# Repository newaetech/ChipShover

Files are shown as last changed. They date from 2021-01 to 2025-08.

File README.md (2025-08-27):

# ChipShover®

ChipShover is an XYZ table &amp; driver, with handy Python interface. It's designed for close analysis of ICs using tools like Electromagnetic Fault Injection (EMFI), EM Probes for side-channel, and more. In both specifications and cost it falls somewhere between between 3D printers & microscope stages.

ChipShover consists of the following main parts:

* Physical XYZ Stage (based on stepper motors)
* Interposers to mount tools onto the stage
* Controller for XYZ stage (based on open-source Marlin firmware)
* Python interface on computer

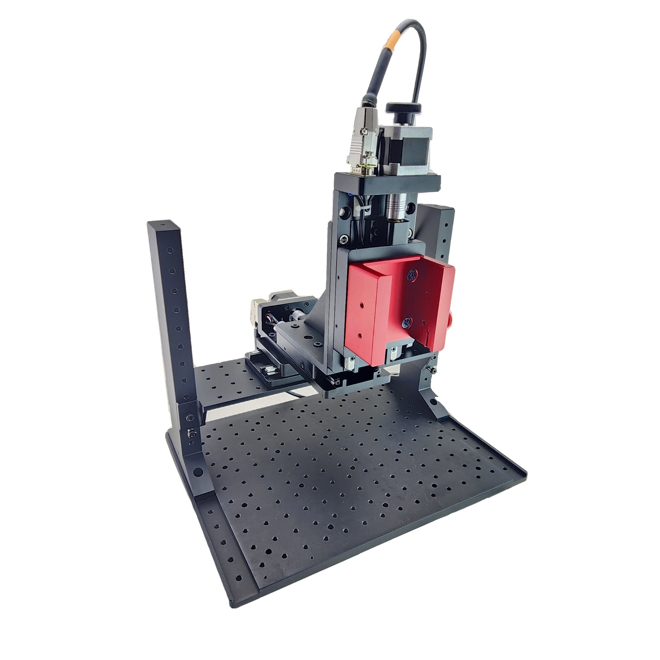
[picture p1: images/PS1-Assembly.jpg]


## Physical XYZ Stage

The physical XYZ stage is designed for two major variants, however you can easily customize it based on tables and parts you have on-hand. These variants are presented to simplify your general choice of options. They are currently called the *medium-resolution* stage (step size of 156.25 nm, backlash/general error around 3um), and a low-resolution stage (step size of 781.25 nm, bkaclash/general error around 50-100 um).

### Medium-Resolution Stage (< 1 um)

The medium-resolution stage is composed of a custom frame and motorized microscope stages. The frame is made entirely of solid machined aluminum.

For easiest setup and best results. This stage is available as part of a Kit from NewAE that also includes our controller, power supply, and helpful accesories. We call it the ChipShover PS1 (Positining system 1). 

### Low-Resolution Stage

The low-resolution stage uses a CNC frame fairly widely available on AliExpress and similar. With this version you must buy the stage yourself - the size and lowish cost ($500) of the stage makes it not worth carrying for NewAE! The cost is significantly lower, with more hassle in the purchasing process and somewhat lower resolution and specifications on the resulting table.

## Interposers

The XYZ stage is designed to fit a variety of tools using a 50x50mm bolt pattern. Currently, this has the following interposers:

* ChipSHOUTER® holder.
* Pen-Style EM probe holder.

The ChipSHOUTER mounting hardware is included in the PS1 kit, otherwise these interposers can be 3D printed or machined from files in the repo.

## Controllers

The controller is based on 3D printer controllers which have extensive community resources behind their hardware and firmware. The ChipShover controller is specifically based on the Arduino DUE, which uses a Microchip SAM3X (we use the similar SAM3U in many of our products already which was our reasoning).

The firmware is open-source and is a [build of Marlin2 with a custom board type](https://github.com/newaetech/ChipSHOVER-Marlin). The board is designed to be the ChipShover-One ($1300 for enclosed & tested unit, lower-cost version planned around ~$350). Other boards such as the [Archim2](https://ultimachine.com/products/archim2) are possible with some limitations (approx $180 for board + some cables needed).

### ChipShover-One

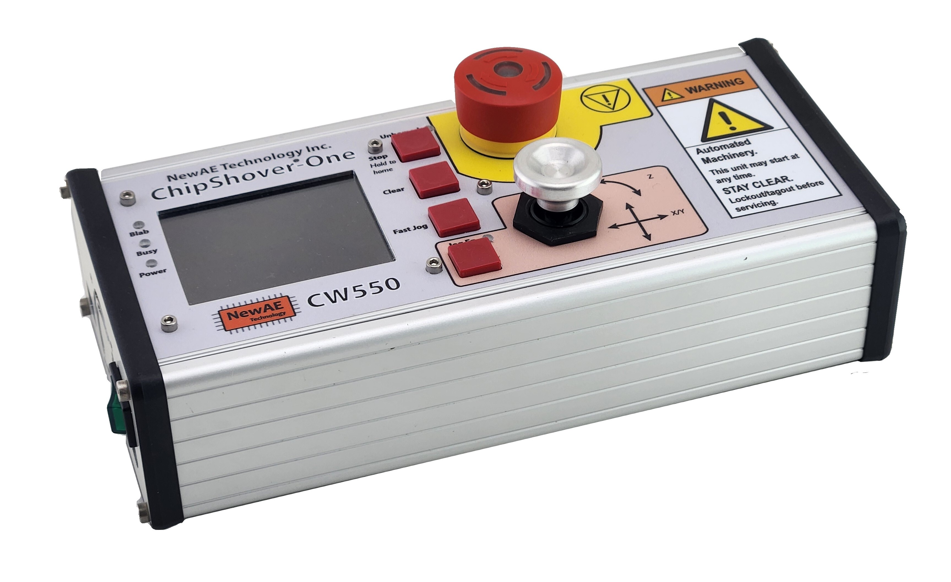
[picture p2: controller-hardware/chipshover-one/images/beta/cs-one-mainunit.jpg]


The ChipShover-One is our own stepper controller. While there are hundreds of already existing controllers out there, we figured why not make it interesting with our own take? Several feature relevant to the ChipShover usage that are not widely available in existing 3D printer driver boards were specifically added:

* 3 endstop inputs per axis (2 endstops, 1 higher-resolution home).
* Swappable driver boards to work with different tables.
* Easy user API over USB (Ethernet optional).
* Higher drive current (~2.4A).
* Extension connectors for each axis (currently RS485 + I2C + single GPIO used for "stop" input).
* Physical E-Stop button that disconnects power to motors.
* User interface including colour LCD.

As there are *hundreds* of low-cost open-source stepper controllers out there, the ChipShover-One hardware is not *currently* released as full OSHW. Schematics and other information *is* available for your use already. As we finish releasing this it's likely ChipShover-One will become more open.

### Archim2

The Archim2 board is an open-source hardware controller board. It is [sold by UltiMachine](https://ultimachine.com/products/archim2) and can be used to make a board that is compatible with the ChipShover Python API.

The primary limitation of the Archim2 is a lower default resolution (~1um) due to the lower drive current, and only being able to use the mechanical endstops for homing. In practice this solution with an Archim2 still has many advantages compared to an off the shelf 3D printer. See more details in the [Archim2 setup folder](controller-hardware/diy-with-archim2).

## Python Interface

A Python interface simplifies use from existing Jupyter notebooks and similar.

Here is an example usage to sweep an IC surface from (10.0, 10.0) to (12.5, 12.5) in 0.05mm steps. Also plunge the Z-axis down to touch a probe to the surface at each location (useful when probe cannot be dragged across surface safely).

	from chipshover import ChipShover

	shv = ChipShover('com3')

	shv.home()

	for x,y in shv.sweep_x_y(10, 12.5, 10, 12.5, step=0.05, z_plunge=1.5):
	    print("At %f, %f"%(x,y))

#### Disclaimers and all that

ChipSHOUTER and ChipShover are registered trademarks of NewAE Technology Inc.

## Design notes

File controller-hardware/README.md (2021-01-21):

# Stepper Controllers



## ChipShover-One

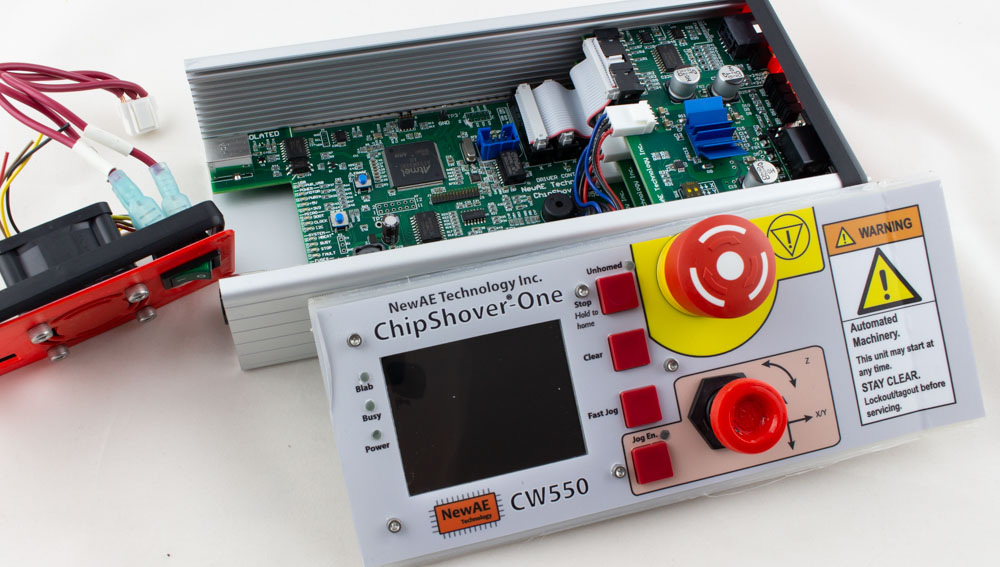
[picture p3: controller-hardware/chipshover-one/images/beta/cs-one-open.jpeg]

*Beta unit shown with 3D printed parts*

ChipShover-One is NewAE Technology Inc's premium control box. When people come into your lab, they will know you mean serious business. We've done things like using a joystick which cost more than the entire BOM of other lower-cost solutions, but has the right "stick feel" compared to cheaper solutions.

But it's not just nice stick-feel that make this such a nice tool - with ChipShover-One you get capabilities like:

* High-power stepper drivers per channel - allows microstepping without losing steps.
* Physical jog stick for X/Y/Z.
* Physical pause/stop button to abort moves *without* killing motor power (device maintains position).
* E-Stop button to abort moves & *kill motor power* (device is no longer accurate).
* Colour TFT Display for feedback on position, motor driver status, etc.
* Active cooling for stepper drivers.
* Python 3 API Interface for usage in Jupyter notebooks.
* Compact desktop size.
* Future upgrades include Ethernet interface for remote control (hardware present but not used).

Beneath the hood, we're worked hard to give you a lot of flexibility that you won't find in proprietary solutions:

* Microchip SAM3X8E (Arduino Due chip) based controller running Marlin2 firmware (open-source)
* Swappable driver boards allow replacement when damaged, or for changing to other motor types (5-phase stepper, DC servo, etc).
* Default driver boards feature:
	* TMC2660 Based 2-phase Stepper Drivers
	* 3 end-stops per channel (min / max / origin) with noise filtering.
	* LED status indicates physical state of each end-stop for help with initial setup.
	* RS485 + I2C + GPIO Extension connectors *per channel*.

The extension connectors allows implementation of additional features, such as adding a "crash detection" probe. This allows the controller to automatically abort a movement if it detects the chip surface contact (**NB: this feature requires you to implement it currently**). They could also allow usage of an external encoder or other feedback.

### ChipShover-One Controller Kit

**$1300 (Estimate)**

* ChipShover-One in Aluminum Enclosure
	* 3x 2-Phase Stepper driver board (CW562) installed for X/Y/Z.
	* 1x 2-Phase Stepper driver board (CW562) spare (for quick replacement if you blow a channel somehow).
* 120W power supply (24V / 5A) with US + EU plugs included
* 3x 1m stepper motor cables
* 3x stepper motor breakout boards (for connecting tables besides the NewAE one)
* 1x stepper motor diagnostic board (allows scoping signals)
* 3x 0.1m extension cables
* 3x 1m extension cables
* 3x extension cable breakout connectors
* 2x spare fuses
* 1x USB 2.0 cable
* 1 year warranty

## ChipShover-Three-Quarters

**$350 (Estimate)**

ChipShover-Three-Quarters is a variant of ChipShover-One for people who want a lower-cost option but most of the core functionality. In order to reduce the cost, this solution does not come with the aluminum enclosure, and instead is designed to have all the boards mounted on the backside of your device (or just on a table). It requires some assembly (making cables, simple soldering, etc) and some parts (switches).

The main *missing* things:

* No enclosure.
* No E-Stop button provided.
* No Joystick (jog buttons instead of joystick - soldering required).
* No cooling fan.
* No 'extension' parts on controller boards (only needed for RS485/I2C extension - not used currently anyway).
* No power supply included (needs 24V @ 2-5A depending on your table).
* No warranty!

We felt that having a medium-cost option was important to make it easier to any researcher to have access to the same controller, as it makes it easier for us to all share results and demos. With ChipShover-Three-Quarters, you still get:

* High-power stepper drivers per channel - allows microstepping without losing steps.
* Physical pause/stop button to abort moves *without* killing motor power (device maintains position).
* Colour TFT Display for feedback on position, motor driver status, etc.
* Python 3 API Interface for usage in Jupyter notebooks.
* LED status indicators of end-stop states (quick troubleshooting!).

The ChipShover-Three-Quarters *is* more than many cheap 3D printer motherboards on account of our lower volume (we test all boards extensively) & the specific features added to be helpful for our ChipShoving use-case.

We have published details of using the ChipShover API with generic motherboards as well so you can also access some ChipShover features from any 3D printer.

The ChipShover-Three-Quarters mainboard is identical to the ChipShover-One, so the same firmware features can be used on either board.

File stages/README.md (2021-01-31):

# XYZ Stages

The mechanical part of the XYZ table is actually the "most boring", because it's well known. XYZ stages are found in applications such as:

* Microscopes
* CNC
* Engravers
* 3D printers

The most accurate system will use some sort of feedback - the most basic would be on the shaft itself (to detect how far we are rotating the leadscrew), the more accurate would be to have real-time information on the position of the table. With closed loop feedback we can achieve very high levels of repeatability.

Currently *all* of the stages we discuss are open-loop, where we use stepper motors in a direct-drive fashion. Achieving a higher resolution is done with a finer leadscrew. You can also gear down the motors to improve resolution, which has some impact on backlash (not an issue if closed-loop, but is an issue if open-loop).

## Stage Calibration

In order to better characterize our stage setup, we set up a laser interferometer. This allows us to achieve very high resolution measurements, which are highly stable and thus can answer questions such as how repeatable a given stage is when moving back and forth many times.

We are using the setup that [Sam Zeloof describes](https://www.youtube.com/watch?v=vPu6lN9yJOY), which can be assembled for much less than an off the shelf unit.

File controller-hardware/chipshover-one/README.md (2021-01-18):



# ChipShover-One

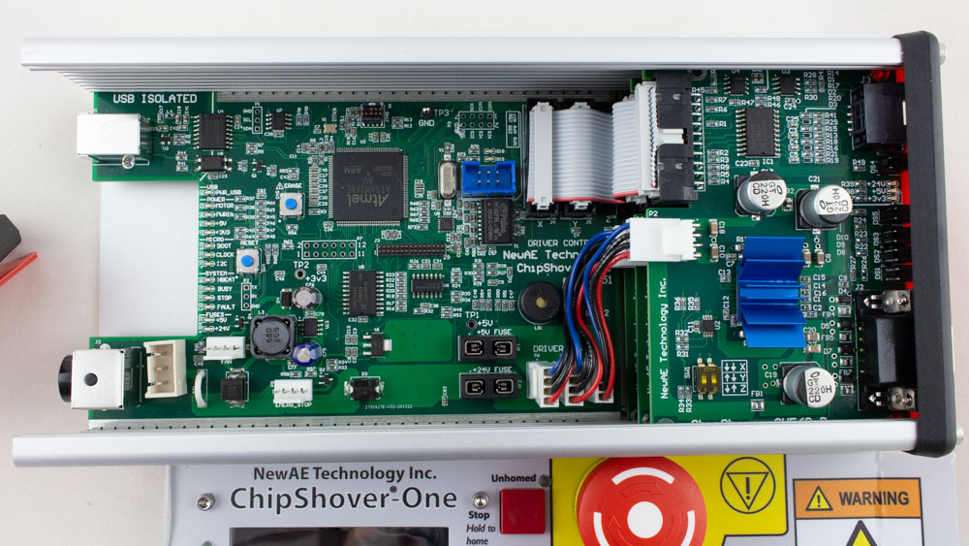
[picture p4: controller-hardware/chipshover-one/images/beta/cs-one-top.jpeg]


## ChipShover-One Specs

## ChipShover-One Front Panel Interface

## ChipShover-One 2-Phase Stepper Drivers

The default (and only) interface board for the ChipShover-One is a 2-phase stepper driver board. Each of the X/Y/Z axis has the same board, visible at one end:

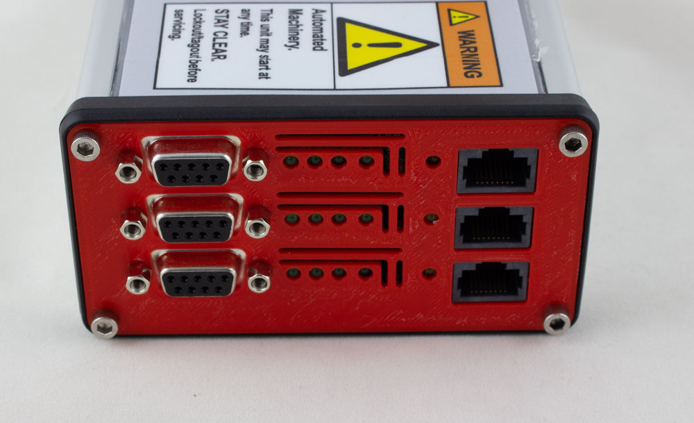
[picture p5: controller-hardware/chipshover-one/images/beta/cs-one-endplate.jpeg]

*Beta unit shown with 3D printed parts*

From left to right, the outputs are:

* DB9 = Axis connection, with stepper + Limit Switches.
* Status LEDs.
* Extension Connector (RJ45 - not ethernet).

### Connecting ChipShover-One to Generic Tables

ChipShover-One is designed to work "out of the box" with NewAE's XYZ table kit. But it also works with almost any other table - in fact, the entire point of ChipShover-One is to make it easy to grab a CNC frame and get a reasonably accurate positioning solution with much less fuss than you have when re-purposing a standard 3D driver controller.

For connecting to other tables, you simply need to wire them to the DB9 connector. For your convenience, a breakout board is included with the main ChipShover-One kit (you can find the schematic + gerbers in this repo as well if you are using ChipShover-Three-Quarters).

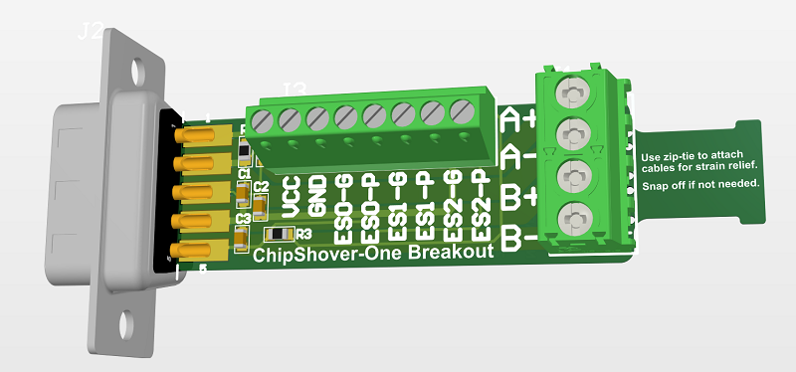
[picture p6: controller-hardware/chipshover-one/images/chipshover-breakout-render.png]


#### Stepper Connections

#### Endstop Connections

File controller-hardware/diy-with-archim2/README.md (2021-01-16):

# Archim2 Driver Option

The Archim2 is a popular open-source hardware driver for a 3D printer. The ChipShover can also be built using this board, although it has some limitations and is **not supported in any official manner**, but instead presented as a community build information.

## Limitations

Archim2 uses the less powerful TMC2130 (1.2A RMS coil current, vs 2.0A RMS coil current on TMC2660 used in ChipShover-One). The primary effect of this is that microstepping may be more likely to lose steps, so a smaller default microstepping value is used. You can however easily adjust this default value, so it's not a hard limitation of the platform.

## Build List

To build the Archim2 option, you will need:

### Archim2 Driver Option

* [Archim2 with Optical End-Stops](https://ultimachine.com/products/archim2). You won't use the end stops, but need the connectors from it.
* 3x Small Heatsinks (see note below).
* 1x 24V, 40mm fan, 2-lead input (suggested: 109P0424H302)
* 1x 3D Printed fan holder
* 2x M4 screws (for fan)
* 2x 4-40 or M3 screws (for fan holder)

#### Heatsinks

Driving the motors *will* require a heatsink on the Archim2. The easiest solution is to buy the widely available "Raspberry Pi Heatsink Pack", such as [FIT0542](https://www.digikey.com/en/products/detail/dfrobot/FIT0542/8549500) for less than $2.

You'll only need the *smallest* heatsink from each pack, so buy 3 packs as you need heatsinks on each X/Y/Z.

#### 24V Fan

The heatsink alone might not be enough, so also plan on getting a 24V fan. We'll use the built-in support for driving a fan (designed for use with the 'extruders').

#### Driver Cables

You'll also need the driver cables for your motor.

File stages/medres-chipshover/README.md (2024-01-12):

# ChipShover Stage

## Rev 2
ChipShover Rev 2 is the production release of ChipShover, shipped from 2024 and onward. This page provides documentation for this production version. There is currently no printed documentation. 

See [Rev2Assembly.md](Rev2Assembly.md "Rev 2 Assembly Document") for assembly instructions.

See [Rev2Instructions.md](Rev2Instructions.md "Rev 2 Instructions Document") for usage instructions.

NOTE: The X stage is mounted backwards in this photo - the assembly instructions above have it the correct way around.

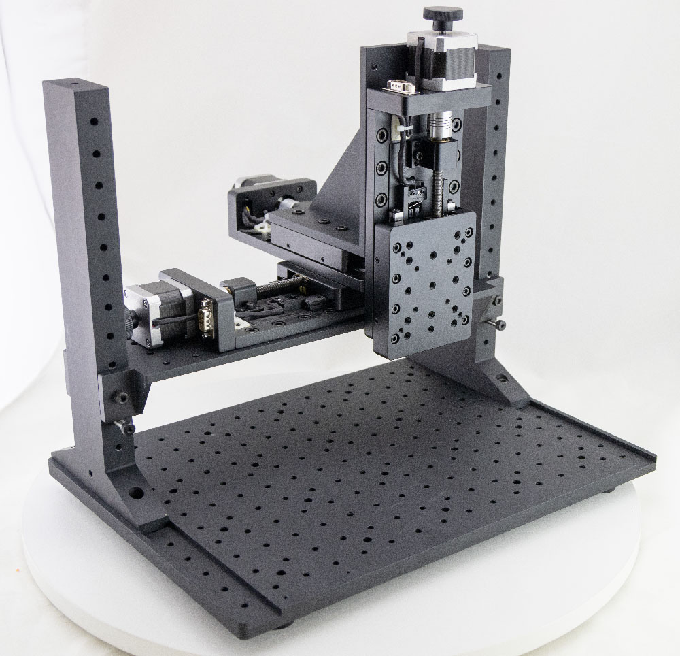
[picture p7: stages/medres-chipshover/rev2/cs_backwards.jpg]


## Rev 1
ChipShover Rev 1 is the initial beta release of the ChipShover. This page provides documentation for these early versions.

See [old_revisions/Rev1Assembly.md](old_revisions/Rev1Assembly.md "Rev 1 Assembly Document") for assembly instructions.

See [old_revisions/Rev1Instructions.md](old_revisions/Rev1Instructions.md "Rev 1 Instructions Document") for usage instructions.

## Rev 0

The first alpha release was called rev0:

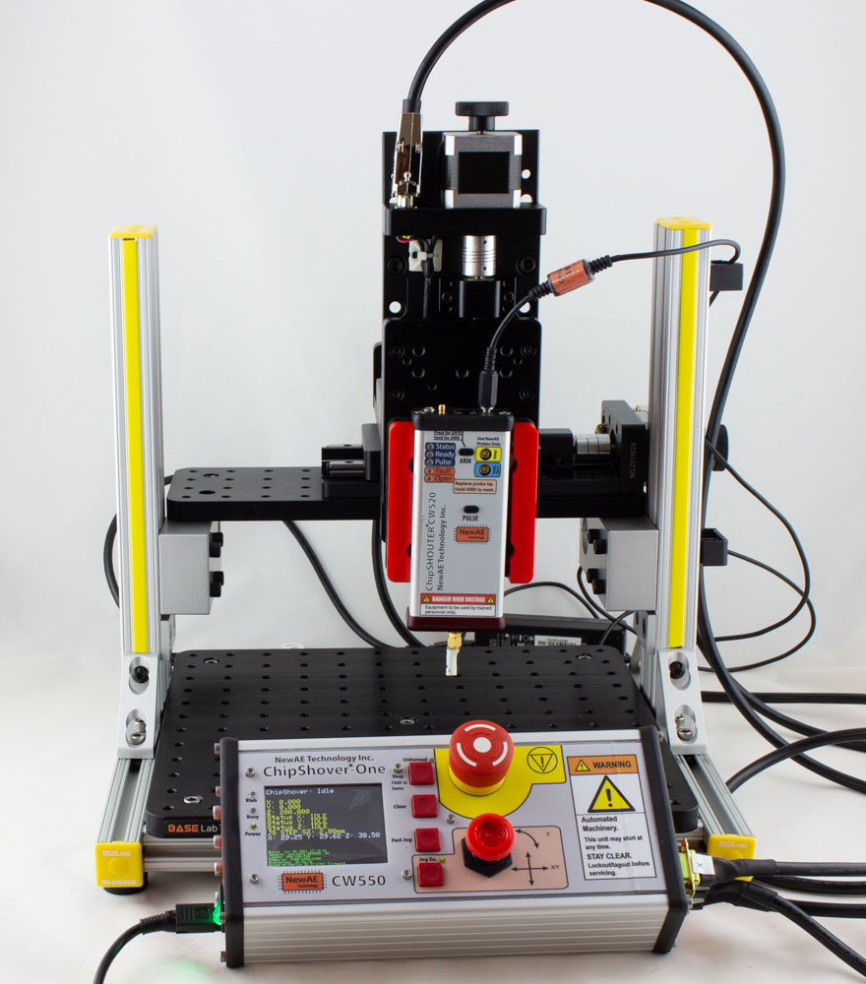
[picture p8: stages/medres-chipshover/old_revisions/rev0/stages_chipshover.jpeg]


This page provides documentation for these early versions:

See [old_revisions/Rev0Assembly.md](old_revisions/Rev0Assembly.md "Rev 0 Assembly Document") for assembly instructions.

See [old_revisions/Rev0Instructions.md](old_revisions/Rev0Instructions.md "Rev 0 Instructions Document") for usage instructions.

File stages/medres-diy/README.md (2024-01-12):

INTERNAL NOTES

NOTE: We **DO NOT SUPPORT** these build instructions. They are left as a community resource, but it in fact may discourage customers from purchasing our solution (if we had any business sense we wouldn't post them in our github). Check carefully for assembly details, as vendor parts may change which stops this solution from working. If you proceed with the self-build solution you are on your own!

Be aware that we've put effort into compiling this list for our own R&D - 

## Frame

### Parts List

Base-Lab-Tools parts:

* 1x [SAB10x30-M](http://www.baselabtools.com/100mm-x-300mm-Solid-Aluminum-Optical-Breadboard_p_397.html) 100mm x 300mm Solid Aluminum Optical Breadboard
* 1x [SAB25x30-M](http://www.baselabtools.com/250mm-x-300mm-x-13mm-Solid-Aluminum-Breadboard-Metric_p_392.html) 250mm x 300mm x 13mm Solid Aluminum Breadboard, Metric

McMaster-Carr Parts:

* 2x [Offset Rail-to-Tube Holder for 2" High Double Rail](https://www.mcmaster.com/47065T89/) - used to hold upper breadboard. This is part number 5415 + 3432 from 8020.net.
* 5x [1"x1" (Single Height) Extrusion, 1 ft](https://www.mcmaster.com/47065T101/) - Bottom Platform.
* 2x [2"x1" (Double Height) Extrusion, 1 ft](https://www.mcmaster.com/47065T107/) - Vertical Rails.
* 2x [1"x1" Diagonal Brace, 6"](https://www.mcmaster.com/47065T186/) - braces vertical rails.
* 1x [Pack of 25 T-Slotted Framing Nut, 1/4"-20](https://www.mcmaster.com/47065T905/).
* 1x [Pack of 1/4"-20, 1/2" long socket head](https://www.mcmaster.com/92196A537/)
* 

### Assembly

Assemble bottom frame using a total of 5x 1-foot extrusion pieces. The basic process:

1. Using T-Slotted framing nuts, fasten three of the extrusion pieces

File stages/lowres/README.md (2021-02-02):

# Low Resolution / Cheapish CNC Frame

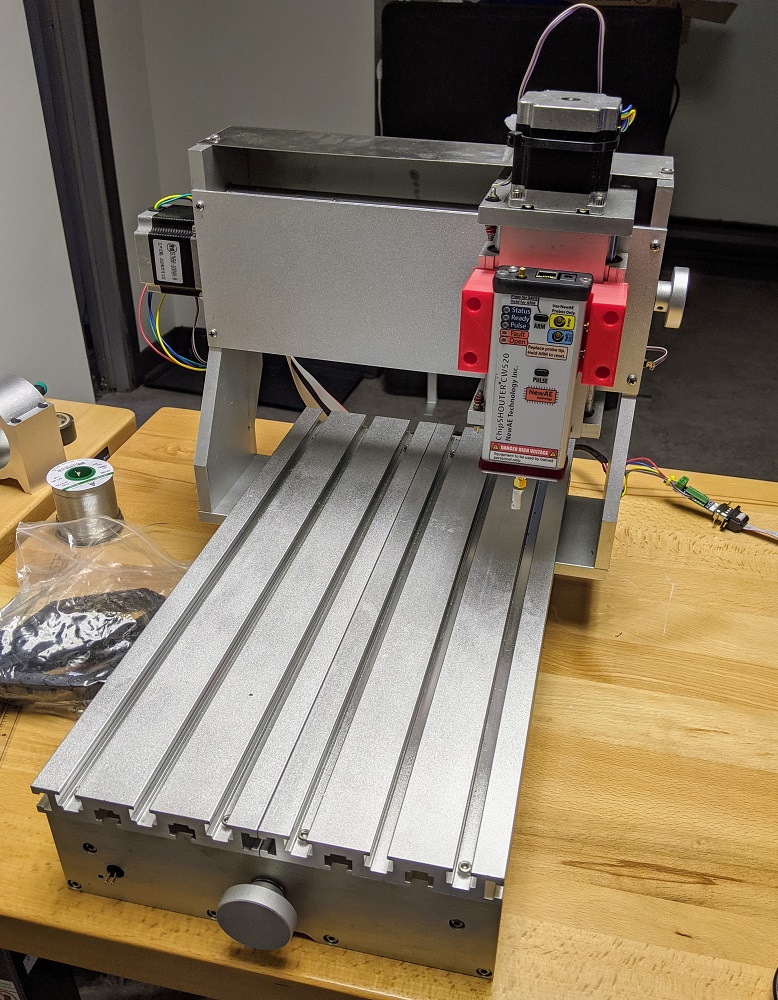
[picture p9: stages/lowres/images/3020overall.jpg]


These instructions show you how to translate a kinda cheap  ($500 + shipping) CNC frame into a high quality EMFI or SCA XYZ scanning solution using the ChipShover-One.

Once you are done you'll have a solution with around 1um resolution (although considerably more backlash & overall error).

## Selecting a CNC Frame

When selecting a CNC frame, we were looking for the following features:

* Bed remains stationary
	* Most 3D printers & CNC move the bed as the Y or X axis - you are certain to have cables attached to your target device, and the target moving increases the chance you'll pull on the target by accident, shifting it's position.
* "Head" holder is removable without affecting Z axis.
* Ships mostly assembled.
	* Low effort setup.
* Includes limit switches (ideally min & max).
	* Some low-cost machines use motor stalls instead of real end stops. ChipShover-One doesn't support this currently.

The Y axis moving is often OK in practice if you are careful with the setup. But as we are trying to build a general setup for your lab environment, we didn't want to worry about this.

The removable holder for the motor/laser is handy as we'll need to 3D print a ChipSHOUTER holder instead (or whatever other probe you want to hold).

## "CNC 3020 frame kit" by L.Y. GROUP CHINA 

The suggested low-res frame is called the "CNC 3020 frame kit". Be sure to get the kit with stepper motors if you want to follow along. The frame I received *didn't* have the L.Y. group silkscreen on the frame - it's not 100% clear if this is a clone or legitimate frame. The specific store I purchased from looked like this:

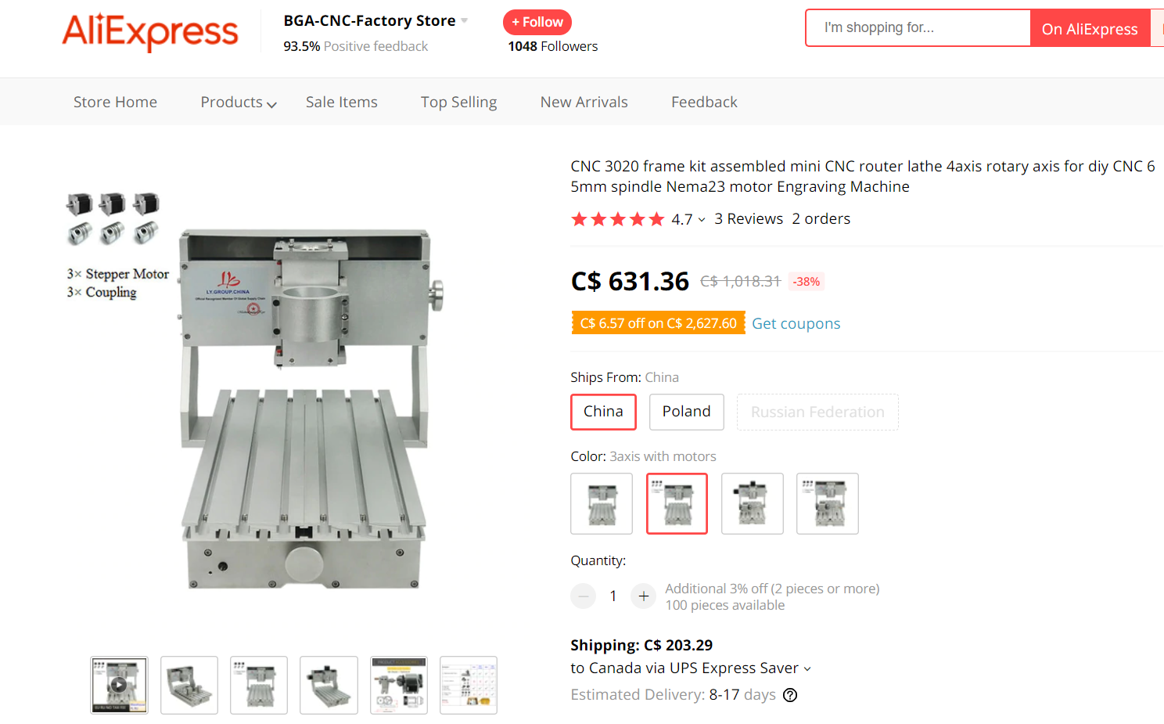
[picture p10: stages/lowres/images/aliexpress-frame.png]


### Frame Assembly

The frame ships assembled, you just have to mount motors on it. To tighten the couplings onto the stepper motors you'll have to remove a few of the aluminum panels.

The frame has a *lot* of grease on it I found - take a rag and clean up some of this.

### ChipShover to Frame Interface

Interfacing the ChipShover to the frame requires you to:

* Connect the stepper drivers.
* Connect the endstops.

This is easily done with the stepper breakout boards, or you can terminate a DB9 cable into the stepper motors & endstops directly.

**WARNING**: The wire shipped with the table for the endstops was amazingly terrible. In addition, the endstop buttons are very cheap and the contacts will very quickly melt into the plastic of the endstop when soldering. You must be **very** careful when soldering to it. I would recommend getting some stranded (not solid core as it needs to flex - don't just steal some wire from a CAT5 cable) & some replacement push buttons.

Where the endstop wire will flex, I fixed the wire to the frame or stepper motor, as shown here:

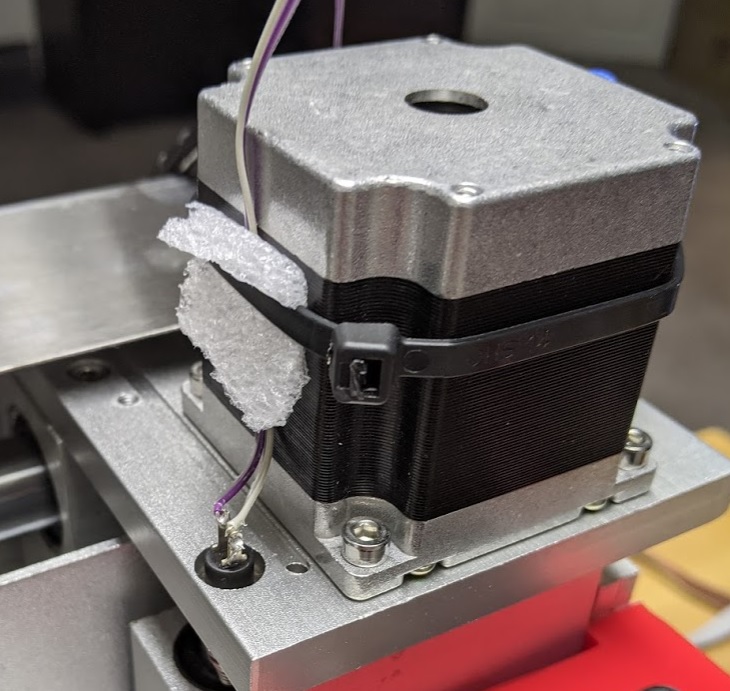
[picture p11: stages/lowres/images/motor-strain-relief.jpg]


When mounting the boards - make sure you don't mount them somewhere that might cause the cables to catch. For example, here is a poor location as the cable may catch when the X axis moves from one side to the other:

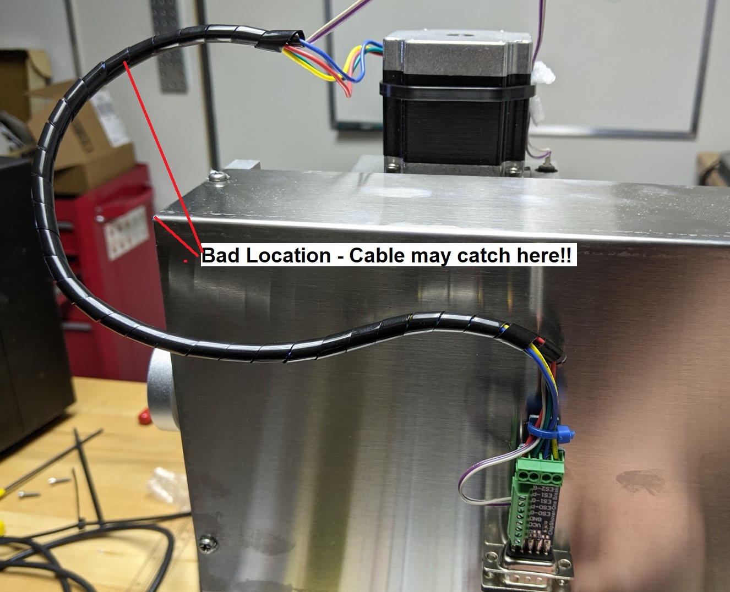
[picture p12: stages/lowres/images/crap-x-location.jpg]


The overall locations I used for this example is shown below:

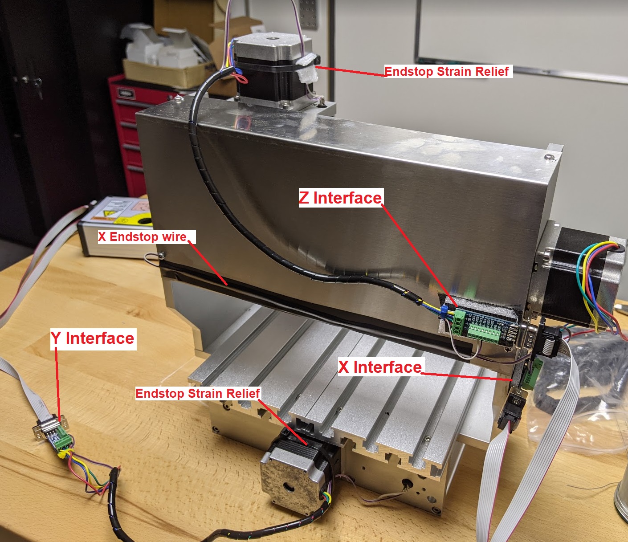
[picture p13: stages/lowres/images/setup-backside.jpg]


Some important setup notes:

* Cables have been cut to length - you don't want a lot of excess cable as that is liable to be caught by something.
* The X endstop wire is taped onto the back cover, and routes to the X interface. ChipShover assumes X=0 is to the right, so we've used that right endstop as the `MIN`.
* The cable covering was provided with the 3020 frame - it's just been cut to each length as needed.
* Interface boards are attached with tape - be very careful they can't fall off, suggest to use Zip-Ties. If they fall off they may **short out and blow up the ChipShover**. 
* Breakout ('interface') boards use a zip-tie to help with strain relief (the breakout board has an area designed for this).

**Z Axis Wiring**:

| Wire | Connect To | Note |
|---|--- |---|
| Red  | A+ | Stepper |
| Green| A- | Stepper |
| Blue | B+ | Stepper |
| Yellow | B- | Stepper |
| Switch | ES1-G | TOP endstop (max) |
| Switch | ES1-P | TOP endstop (max) |

Be sure to secure the endstop cable so it doesn't pull the wires from the switch.

**X Axis Wiring**:

We reverse the X axis stepper so it goes "backwards" - you can do this in firmware too.

| Wire | Connect To | Note |
|---|--- |---|
| Green  | A+ | Stepper - reversed! |
| Red | A- | Stepper - reversed! |
| Blue | B+ | Stepper |
| Yellow | B- | Stepper |
| Switch | ES1-G | RIGHT endstop (min) |
| Switch | ES1-P | RIGHT endstop (min) |

The right endstop (right when looking from the FRONT) is used, so we run the wire across as shown in the previous photo.

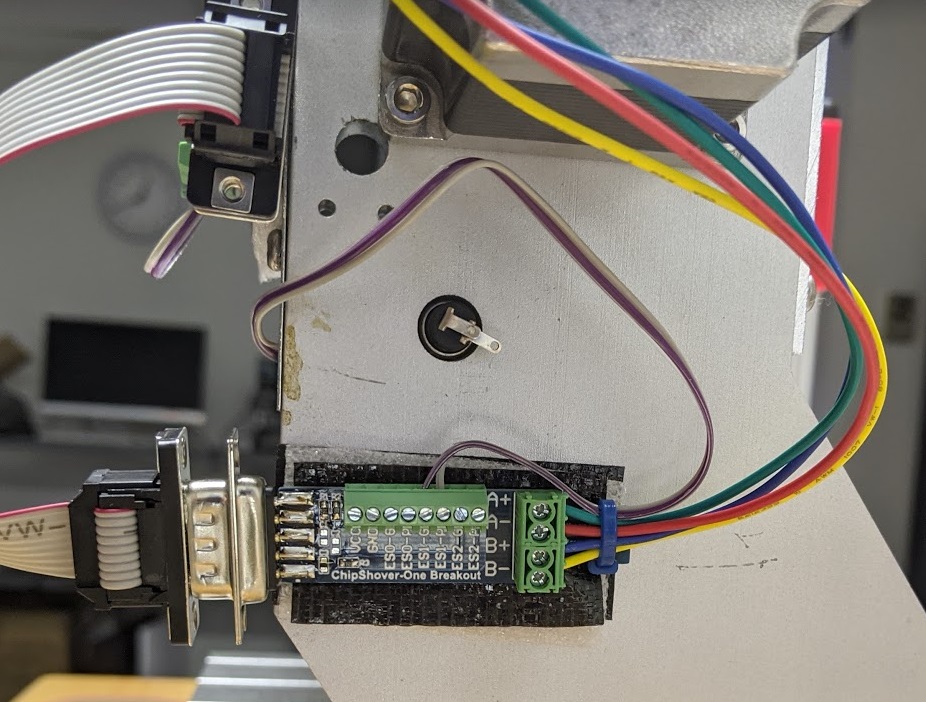
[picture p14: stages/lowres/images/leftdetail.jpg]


(The endstop in the photo was rather smushed from shipping)

**Y Axis Wiring**:

| Wire | Connect To | Note |
|---|--- |---|
| Red  | A+ | Stepper |
| Green | A- | Stepper|
| Blue | B+ | Stepper |
| Yellow | B- | Stepper |
| Switch | ES1-G | REAR endstop (min) |
| Switch | ES1-P | REAR endstop (min) |

Be sure to secure the endstop cable so it doesn't pull the wires from the switch.

### Checking Interface

The ChipShover-One status LEDs will tell you the status of each end-stop. The lights should go *off* when the endstop is pressed with the default configuration.

### ChipShover Settings

* X/Y axis is 1605 ball screw = 1280 steps/mm (@32 microsteps)
* Z axis is 1204 ball screw = 1600 steps/mm (@32 microsteps)

You can configure this with:

```
shvr.set_stepsmm(1280, 1280, 1600)
```

Or you can pass this as an option to the initial object:

```
shvr = ChipShover(comport="com3", stepsmm=(1280, 1280, 1600))
```

You can alternatively rebuild the firmware with your specific table defaults (eventually we will support storing this to EEPROM, not possible yet).

### ChipSHOUTER mounting bracket

You can 3D print a mounting bracket that replaces the spindle holder.

* Remove the M4 bolts holding the motor/spindle holder.
* 3D print the model in this repository - there are two versions of this holder.:
	* "No Hardware Needed" does not require any hardware.
	* "Hardware Needed" version uses heatset screw inserts.
* Bolt the holder back into position using M4-16 bolts. You may need to loosen the Philips screws holding the aluminum Z-ballscrew cover plate, as it's a very tight fit over the cover plate, and there is some play in the cover plate position once the screws are loose. Tighten the Philips screws back after. 
* Use a 6-32-1/2" bolt to secure the ChipSHOUTER.

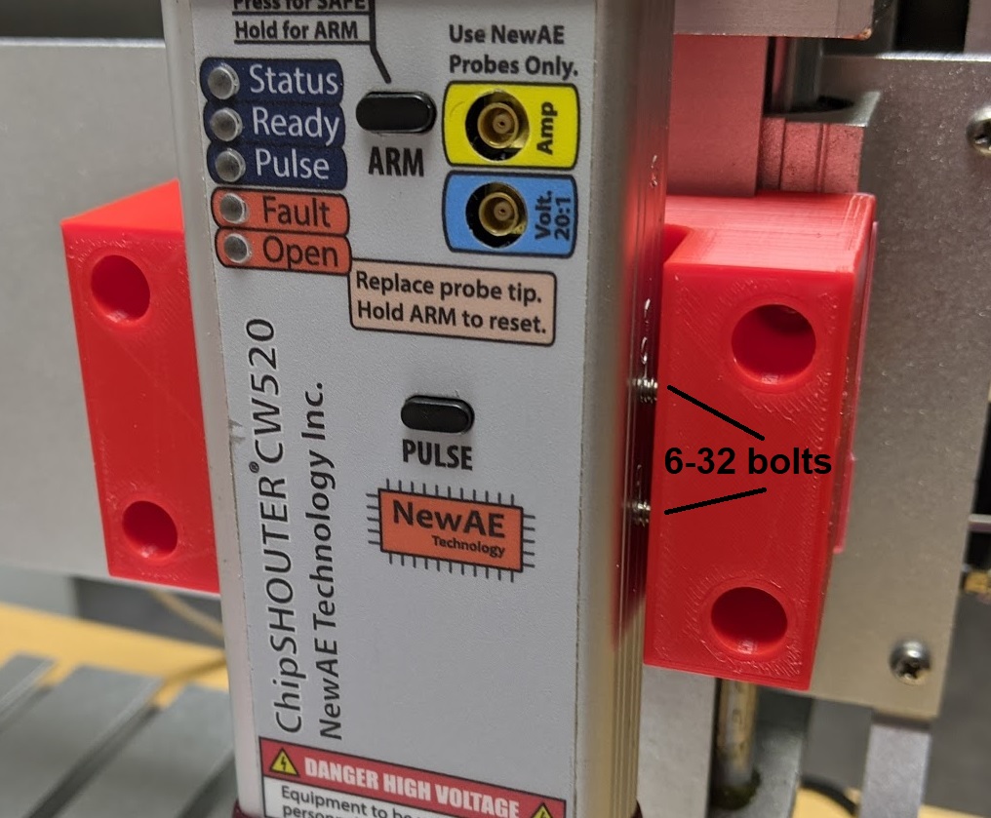
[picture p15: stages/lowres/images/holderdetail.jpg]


The 6-32 bolt will leave a mark on the side of the ChipSHOUTER enclosure:

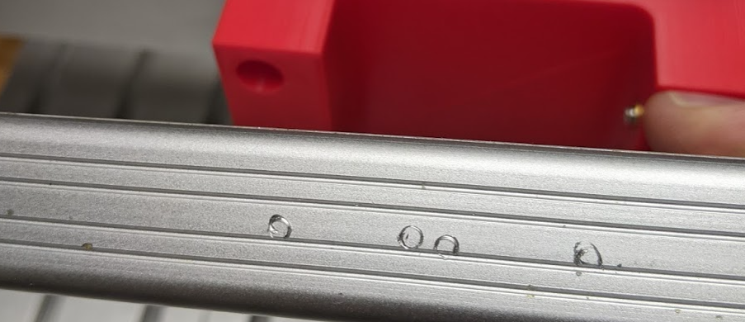
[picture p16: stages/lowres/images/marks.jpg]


You can use a piece of metal to push against, or use the brass-tip bolts (link below) which leaves a smaller mark.

When 3D printing, I was able to get away without adding support structure:

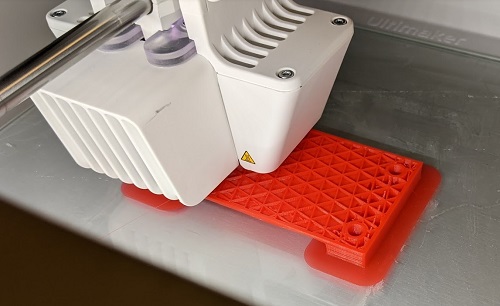
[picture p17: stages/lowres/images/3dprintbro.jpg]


If using the hardware needed version, sink a 6-32 = 0.281" length flanged insert, such as [McMaster-Carr 97171A140](https://www.mcmaster.com/97171A140/) using a soldering iron.

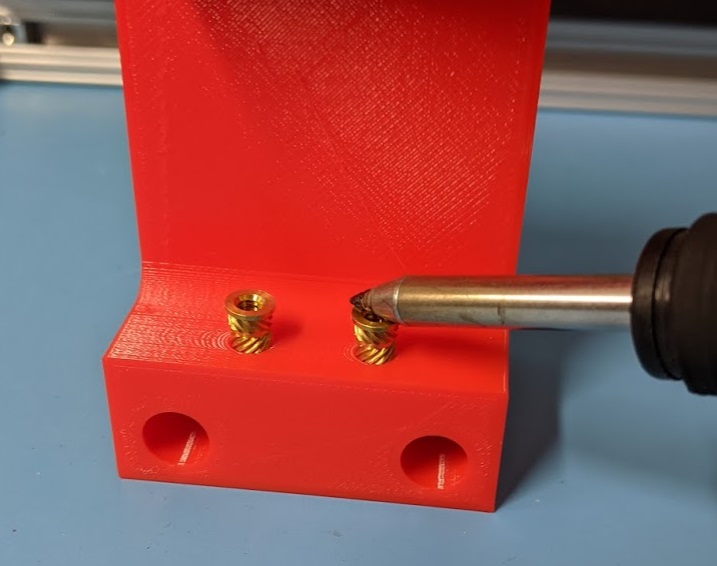
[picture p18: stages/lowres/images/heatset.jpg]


You'll then need a 6-32-1/2" bolt to secure the ChipSHOUTER. You way wish to get a softer tip option, such as [McMaster-Carr 90299A145](https://www.mcmaster.com/90299A145/). This will leave a smaller mark on the ChipSHOUTER enclosure.

## Accessories

For mounting your board to your table, you can use the ChipShover Mounting Kit. This includes T-Slots that will fit this table, and allow you to use the interface feet.

Alternatively, you can 3D print mounting brackets that may fit your specific board & table setup.

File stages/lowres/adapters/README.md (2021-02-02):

# ChipSHOUTER to 3020 Stage Adapter

These adapters are mounted in place of the spindle holder. It should fit the default M4 bolts used on the frame. Remove the spindle holder, and bolt on the ChipSHOUTER adapter.

If you wish to use a screw insert you can print the HardwareNeeded version, otherwise print the NoHardwareNeeded version.

## Model Notes

The two versions of the model are the same, with the inner diameter of the hole changed:

**For 6-32 insert:**
  Hole diameter = 4.90 mm

**For 6-32 screw (self-tapping mode):**
  Hole diameter = 3.20 mm

Note that 3D printing results in a smaller hole size, so the above sizes already account for that. The end hole sizes should be:

For 6-32 insert: 4.8mm

For tapping a 6-32 hole: 2.7mm

The 6-32 hole is slightly larger in this plastic as we basically self-tap it, but if you were making this out of aluminum & using a tap the above is the correct size.

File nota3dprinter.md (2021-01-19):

# ChipShover is not a 3D Printer Controller

ChipShover is missing some key features compared to a 3D printer motherboard:

* Only 3 axis stepper controllers possible (no Extruder axis).
* No heater channels.

The cost of the ChipShover-One *far exceeds* a comparable 3D printer motherboard, as the "device positioning" market is much smaller and thus we cannot hope to achieve the volume of 3D printer drivers.

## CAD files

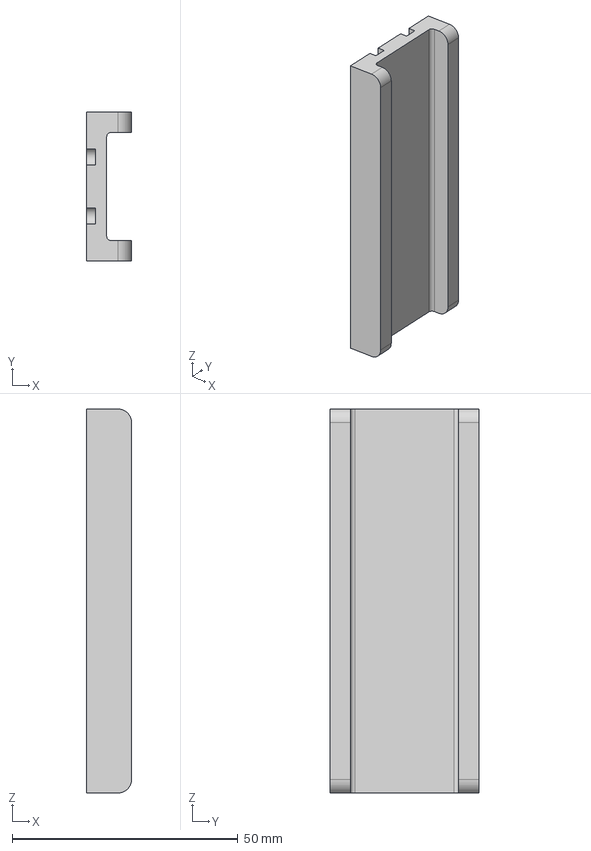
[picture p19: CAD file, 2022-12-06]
chipshouter_adapter/50mm_mounting_pattern/cnc_multipart/cnc holder multipart slides.step
10.0 x 33.0 x 85.0 mm

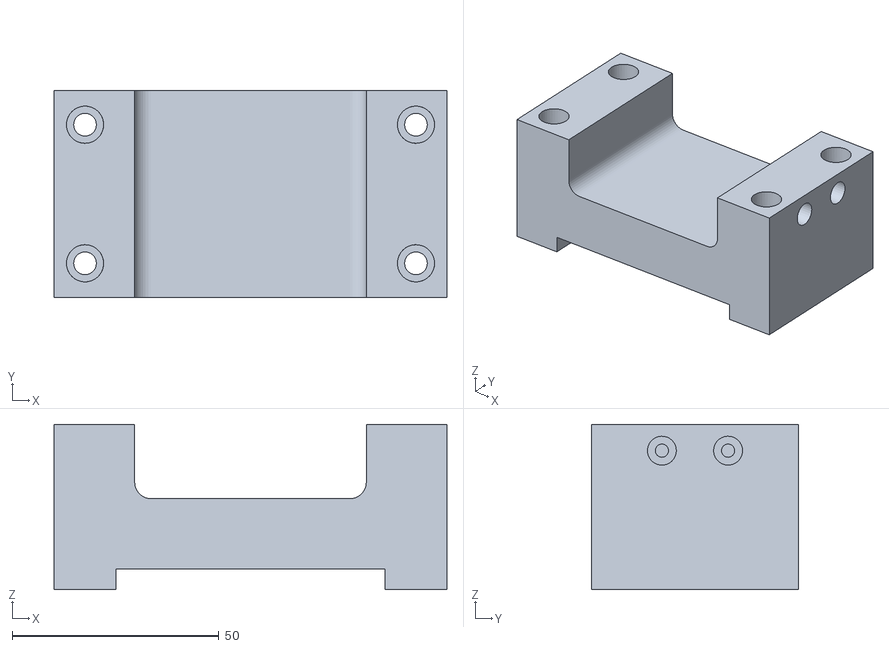
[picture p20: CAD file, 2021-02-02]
stages/lowres/adapters/3020Table_ChipShouterAdapter_NoHardwareNeeded.stl
95.0 x 50.0 x 40.0

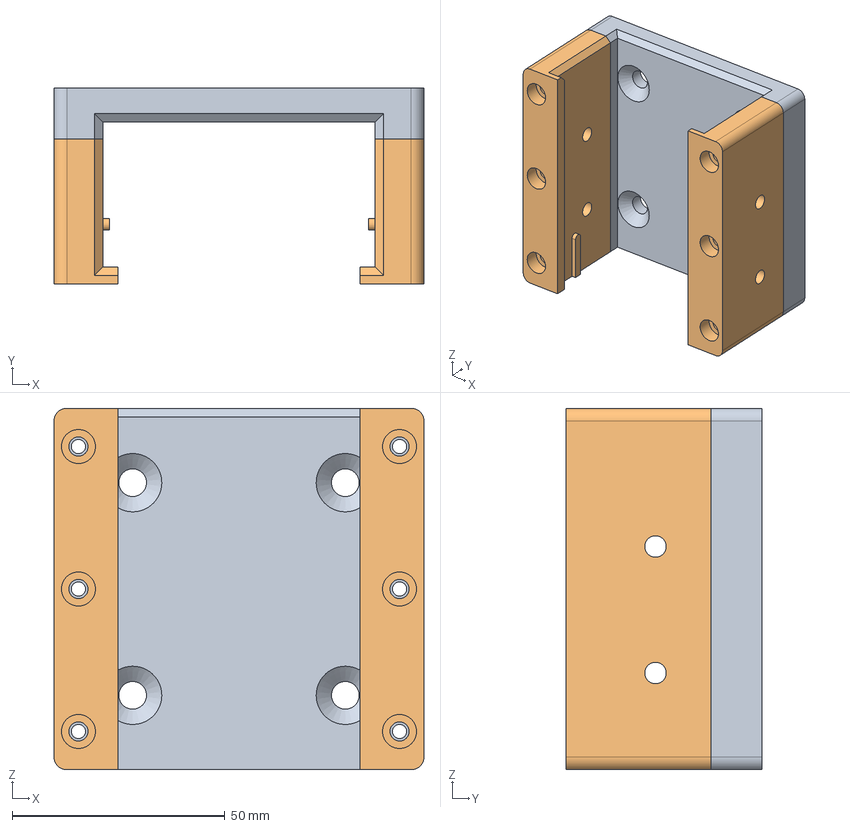
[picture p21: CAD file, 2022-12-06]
chipshouter_adapter/50mm_mounting_pattern/cnc_multipart/cnc holder multipart.step
87.0 x 46.0 x 85.0 mm

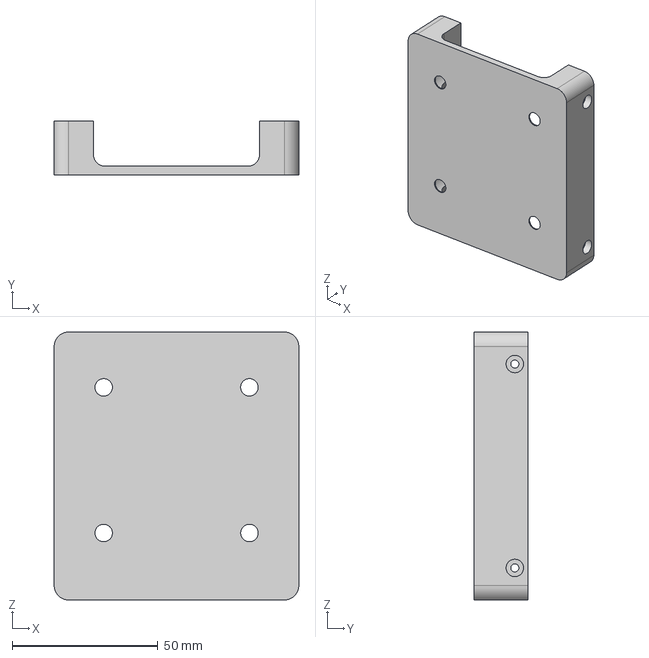
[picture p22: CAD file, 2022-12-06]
chipshouter_adapter/50mm_mounting_pattern/3dprinted_simple/chipshouter mount - M3 or 4-40 holding bolt.step
84.0 x 18.5 x 92.0 mm

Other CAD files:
stages/lowres/adapters/3020Table_ChipShouterAdapter_HardwareNeeded.stl
chipshouter_adapter/50mm_mounting_pattern/3dprinted_simple/chipshouter mount - M3 or 4-40 holding bolt.f3d
chipshouter_adapter/50mm_mounting_pattern/3dprinted_simple/chipshouter mount - M3 or 4-40 holding bolt.stl
chipshouter_adapter/50mm_mounting_pattern/cnc_multipart/cnc holder multipart slides.f3d
chipshouter_adapter/50mm_mounting_pattern/cnc_multipart/cnc holder multipart slides.stl
chipshouter_adapter/50mm_mounting_pattern/cnc_multipart/cnc holder multipart.f3d
chipshouter_adapter/50mm_mounting_pattern/cnc_multipart/cnc holder multipart.stl
stages/lowres/adapters/3020Table_ChipShouterAdapter_HardwareNeeded.f3d
stages/lowres/adapters/3020Table_ChipShouterAdapter_NoHardwareNeeded.f3d

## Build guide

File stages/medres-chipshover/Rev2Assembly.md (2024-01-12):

# Medium Res Stage - Rev 2 Assembly

NOTE: These are draft instructions, so images etc will be improved in the released version! We have left these here due to some delays in production & our desire to avoid delaying shipping hardware just to finish the instructions themselves.

## 1. Remove Base & Remove Shipping Screws

The one box contains a few parts & subboxes. Remove these carefully, and then find the base. The base has the X stage preinstalled, but the Y and Z stage are strapped to the base for transit.

Carefully place the base on the table, it should look like the following image. Note the 8 bolts (four per stage) which are highlighted below, these are shipping bolts which will need to be removed:

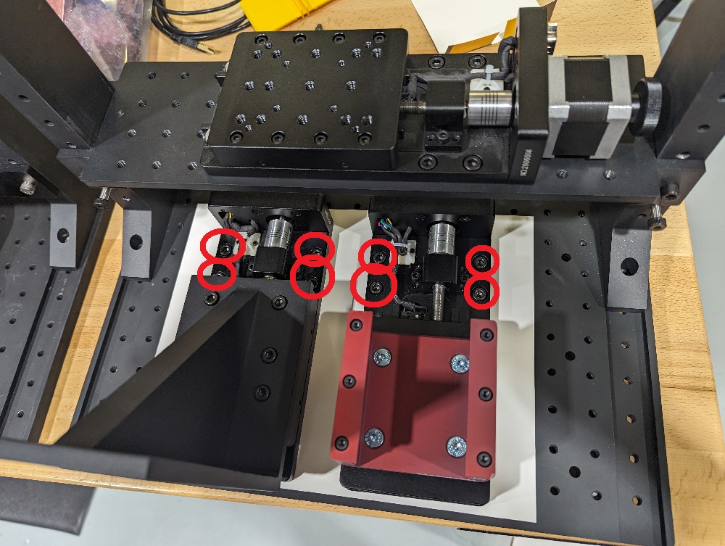
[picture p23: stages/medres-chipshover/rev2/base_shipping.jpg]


The left stage is the Y stage, it includes the black Z-stage mounting bracket. The right stage is the Z stage, it includes the ChipShover holder.

You may need to use the manual adjustment knob on the end of the stage stepper motor to adjust the stage forward to access the bolts clearly.

To remove them, use the provided M5 ball-end driver. The bolts are M6x10 bolts, and you will reuse them for mounting the stages. Remove all the bolts now, but you can leave the stages sitting on the protective cardboard sheet.

## 2. Mount Y stage.

You will need to use the thumb wheel to move the Y stage forward until all 8 mounting holes are exposed:

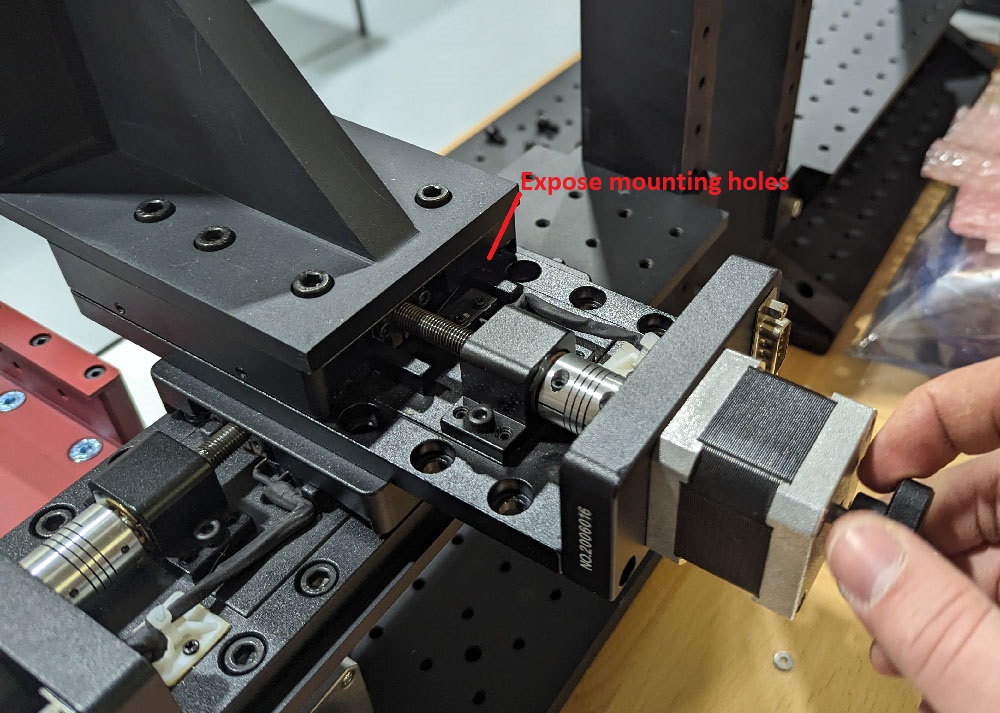
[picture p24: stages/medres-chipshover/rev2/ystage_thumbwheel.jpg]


The Y stage includes the Z-stage mounting bracket. Using only 3 M6x10 bolts, mount that stage to the X stage as shown below (note one hole cannot accept a screw). DO NOT use any longer than M6x10 bolts!

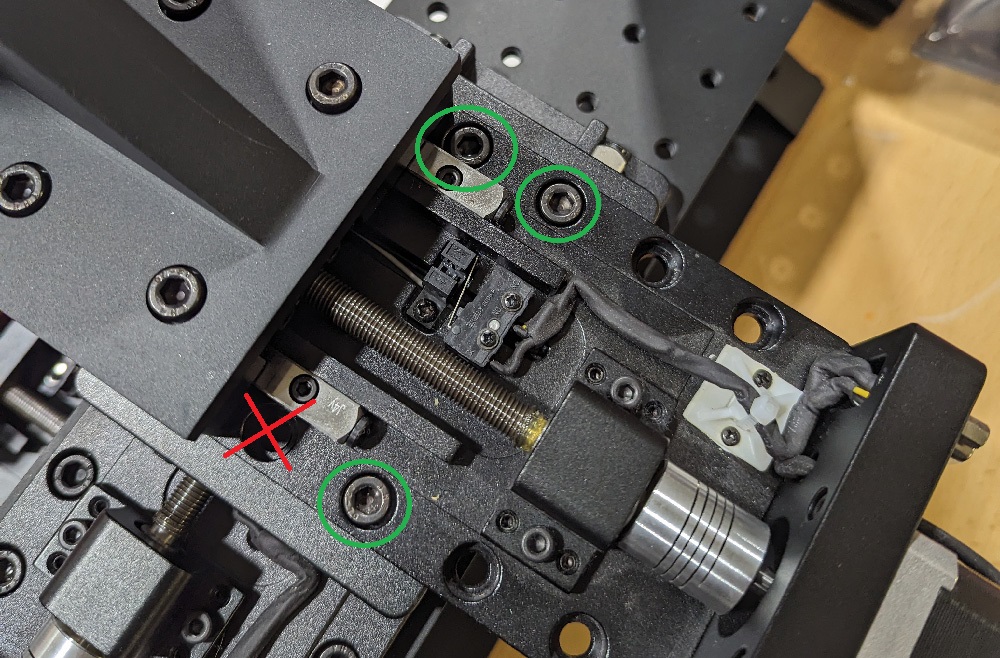
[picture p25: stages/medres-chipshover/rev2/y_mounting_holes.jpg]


## 3. Mount Z Stage

You can now mount the Z stage. You can adjust the position of it, but is suggested as shown here, using these 8 holes towards the bottom of the mount, and leaving the top 4 holes unused:

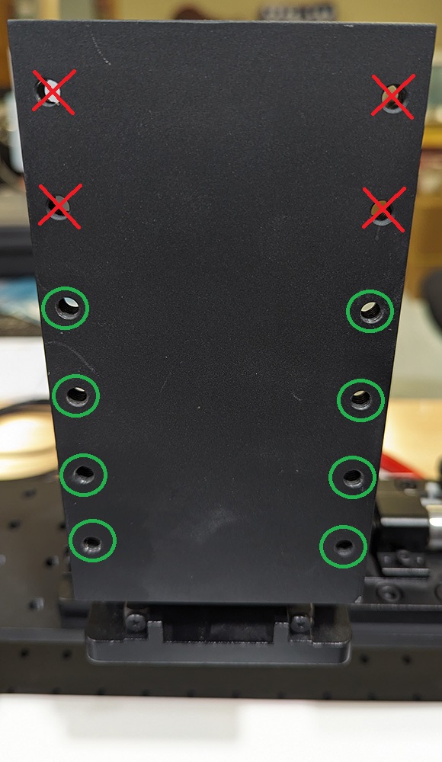
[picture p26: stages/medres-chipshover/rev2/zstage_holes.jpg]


This will look like the following when mounted:

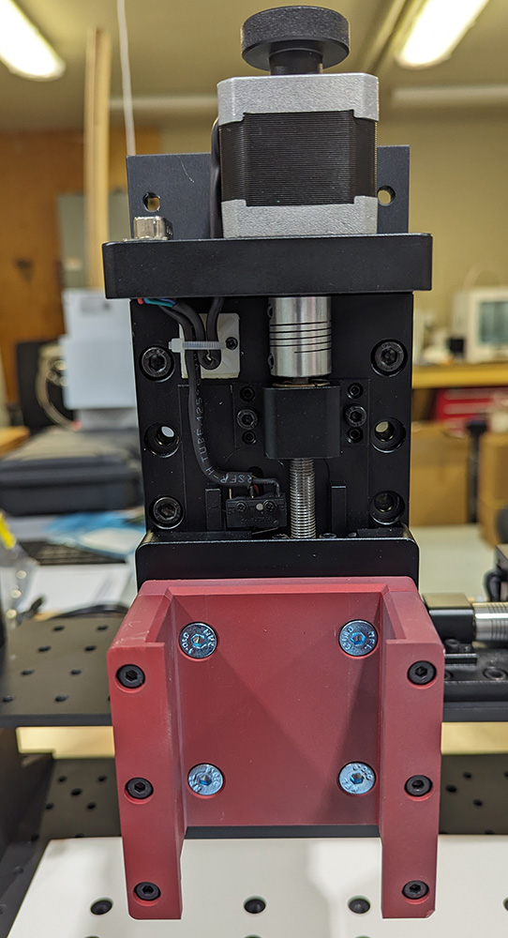
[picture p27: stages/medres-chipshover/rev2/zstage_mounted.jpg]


You may wish to start only with mounting a couple M6x10 bolts, but all M6x10 bolts can be mounted on this stage if you wish.

## 4. Connect Stepper Cables

The stepper motor cables are all standard DB-9 straight-through cables. The provided cables are 22AWG cables allowing a more powerful drive, although we have tested with standard 26AWG IDC cables successfully. Thus if you require extensions or replacements, and off the shelf cable should work.

Due to the spacing at the ChipShover controller the ChipShover mating side cannot use a backshell. Thus you may be limited to IDC style cables for off the shelf cables.

The X/Y/Z/ axis cables are electrically identical, but with different backshells to fit the stage orientation more cleanly. To connect them:

1. Connect each cable to the DB9 connector on each stage. The Z axis connector is straight up and the cable should be routed to a cable mount, the X and Y axis cables are right-angle and will route the cable downward (Y-axis) or upward (X-axis) as appropriate for the best install.
2. Tighten screws on the stage end connector. Use provided screwdriver if required (see tool kit).
3. Connect the other end of each cable to the ChipShover controller - the captive screws need to be tightened to mate the cables.

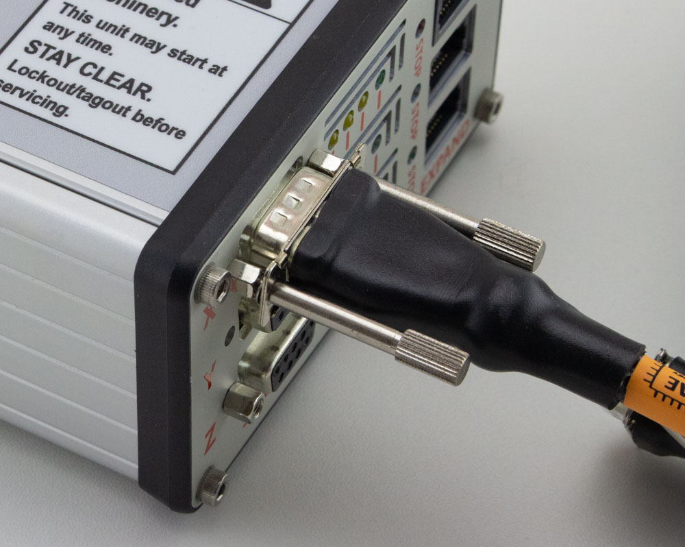
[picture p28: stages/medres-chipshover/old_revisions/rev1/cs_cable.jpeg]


4. The straps which were used for holding parts of the ChipSHOUTER holder in can be used as cable straps. To do this, pass a M6x10 bolt through the end of them, and bolt on an appropriate part of the table. The exact setup will depend on where you position The ChipShover-One Controller:

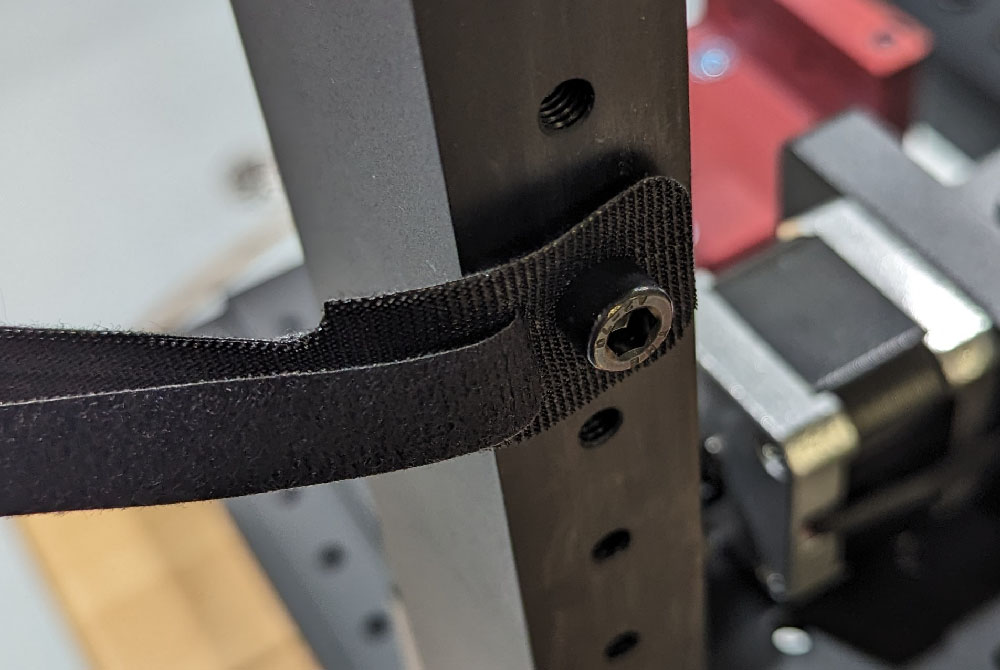
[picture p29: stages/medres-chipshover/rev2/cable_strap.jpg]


	**HINT: If you you need to remove the captive screws from the cable on the ChipShover-One controller end, do this by holding the retaining washer with pliers and "backing out" the bolts.**

## 10. Optional - Test Table

At this point you can test the table before mounting the ChipSHOUTER. To test the table stand-alone:

1. Connect the power supply (4-pin mini-DIN).
2. Turn the power switch on - the switch should illuminate green. If the switch does not illuminate check the power supply.
3. The ChipShover should boot & display status information.
4. Release the E-Stop button by *Rotating it clockwise*, as the E-Stop may have been engaged during shipping.
5. Hold the "stop / home" button for 3-4 seconds - the ChipSHOVER should start the homing operation. You can release the button once it starts the homing operation.
6. **If the homing operation is failing (such as not detecting end-stops) press the E-Stop button immediately**.
7. Press the "Jog En" button to enable the joystick. You will see the Jog En light turn on.
8. Move the joystick in X & Y, and rotate it for Z. The current firmware moves by a fixed amount for each time period (this interface will be adjusted in the future). You can also hit the 'Fast Jog' button which changes the step size.
9. Power off the ChipShover & complete the rest of the steps.

## 11. Add ChipSHOUTER Mounting Bracket

The ChipSHOUTER mounting bracket fits onto the Z axis stage, and is pre-installed for shipping. You can move it to be mounted "lower" on the Z stage, where only the upper 2 bolts are used which provides more clearance if you wish:

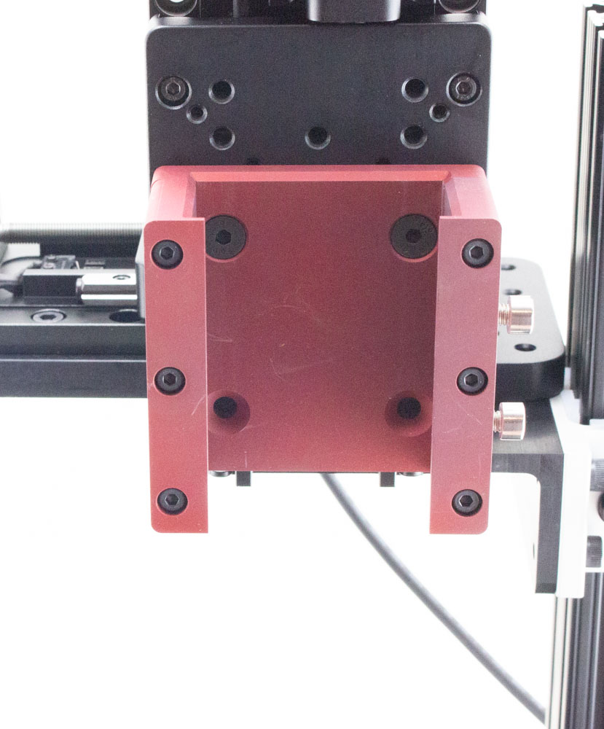
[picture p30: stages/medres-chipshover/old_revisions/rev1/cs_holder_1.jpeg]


Be sure to check you have sufficient clearance for the power & other connectors on the top-side of the ChipSHOUTER. If the ChipSHOUTER is mounted too high, it will cause a collision with the ChipSHOUTER cables and top of the stage.

The beveled end of the mounting bracket faces up.

## 12. Mount ChipSHOUTER

To mount the ChipSHOUTER into the bracket, use the two sliders on the side of the ChipSHOUTER. They should be positioned such the stops in the bracket will prevent the ChipSHOUTER from falling too low:

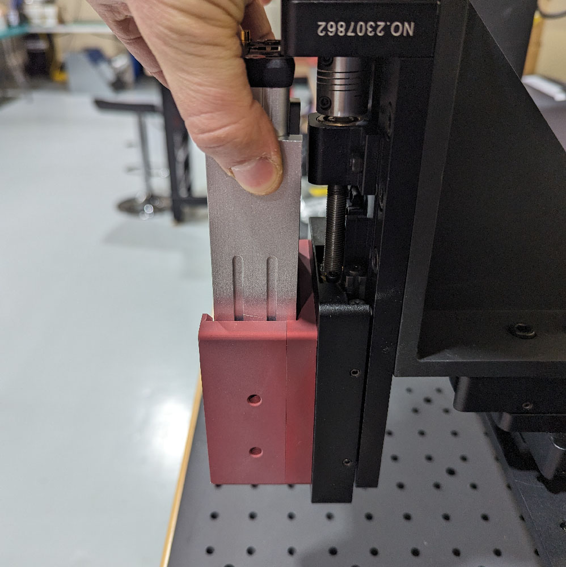
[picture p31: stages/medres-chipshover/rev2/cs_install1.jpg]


To fix the position of the ChipSHOUTER, snug the thumbscrews that hold the sliders in position **while holding the ChipSHOUTER and sliders from below**:

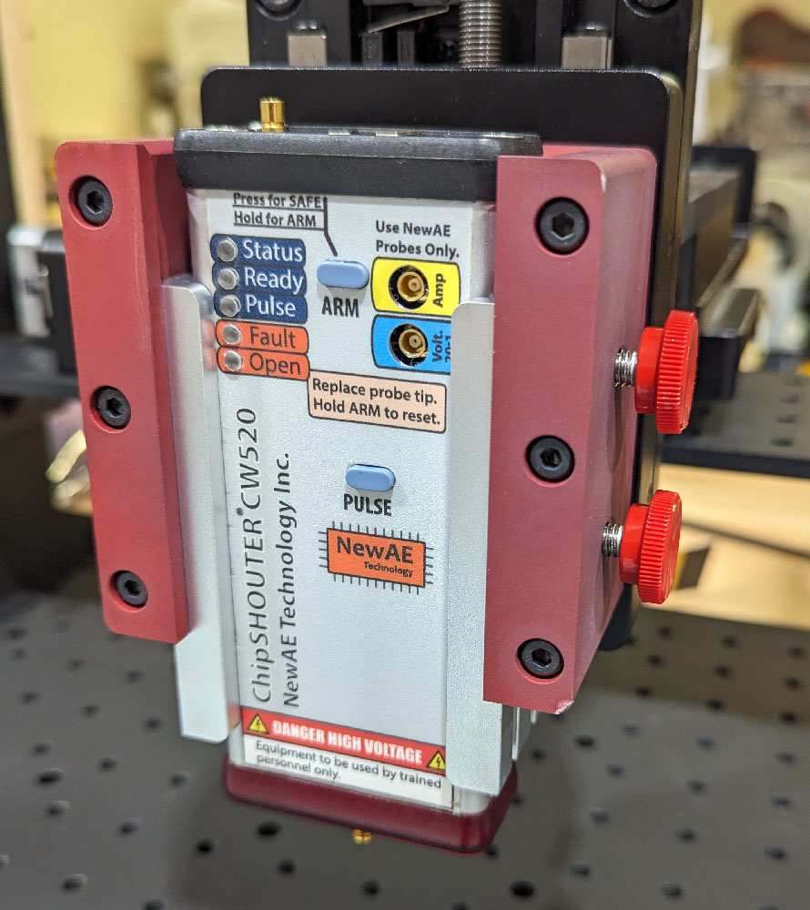
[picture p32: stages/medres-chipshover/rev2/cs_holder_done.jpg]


Depending on your use-case, you might want to leave the bolts only tight enough to hold the bracket secure, but still loose enough such the ChipSHOUTER can slide if you accidentally drive it into your chip.

The bolt mounting allows you to quickly adjust the spacing of the ChipSHOUTER to compensate for various height boards you mount.

**NOTE:** You also may want the ChipSHOUTER at the "lower limit" of travel, such that it cannot drop any further. This prevents the ChipSHOUTER from dropping suddenly if the bolts loosen due to vibration of the table.

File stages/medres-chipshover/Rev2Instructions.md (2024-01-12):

# Medium Res Stage - Rev 2

REV2 is the production release of the ChipShover platform.

## Stage Assembly & Setup

See the [Rev2Assembly.md](Rev2Assembly.md "Rev 2 Assembly Document") for details of the assembly process.

## ChipShover Python Interface

See [chipshover.readthedocs.io](https://chipshover.readthedocs.io/) for the full Python interface details.

## Adjusting Coarse Position

You will have to adjust the position of the ChipShover XYZ stages in a "coarse" fashion to get the ChipShover 50mm travel range to be within the area of your interest. 

### Y Adjustment

To adjust the Y position, remove the four bolts at the base of the uprights. You can then slide the uprights forward & reinstall and retighten the bolts.

### Z Adjustment

The Z adjustment is done by sliding the entire X table upward. In doing this, note the following:

1. You may need to loosen the bolts securing the uprights. The tight fit of the X stage carrier means it may not easily move without loosening these bolts.

2. There are a set of "safety bolts" beneath the carrier. ALWAYS move these bolts one at a time first when moving the stage. For example, when moving the stage higher, one of these bolts is moved (it only needs to be finger tight) while holding the stages with your hand, as shown here:

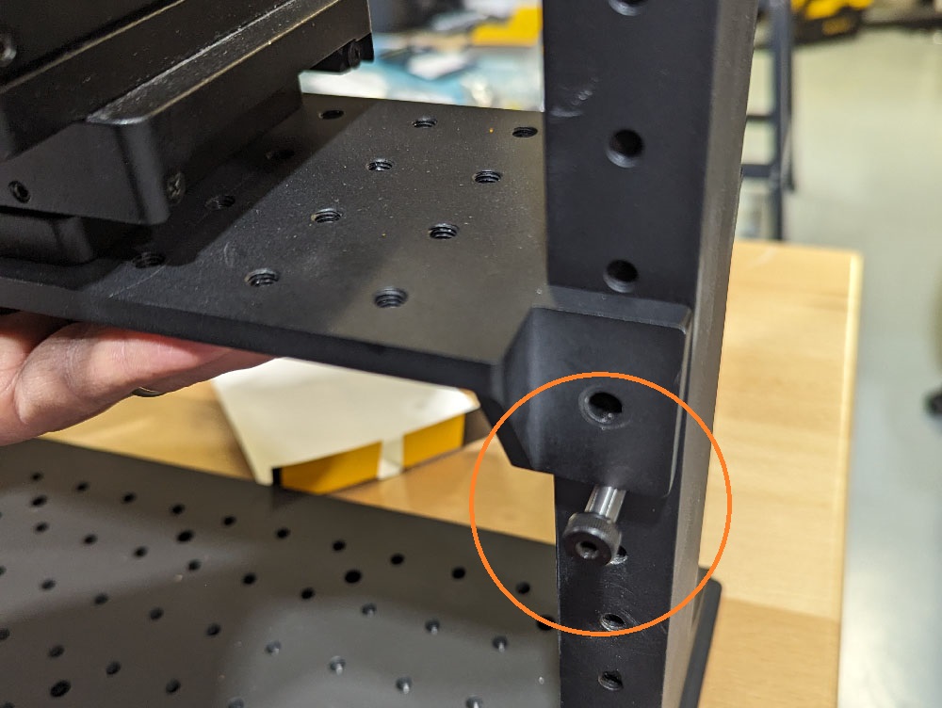
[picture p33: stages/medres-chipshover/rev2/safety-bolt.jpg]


### Board Mounting Kit (PCB Paws)

We provide a board mounting kit, which consists of three pieces:

* Adjustable M6/slot to 4-40 base
* M6 mounting bolt
* 4-40 standoffs

This allows you to mount boards to the base, as in this example:

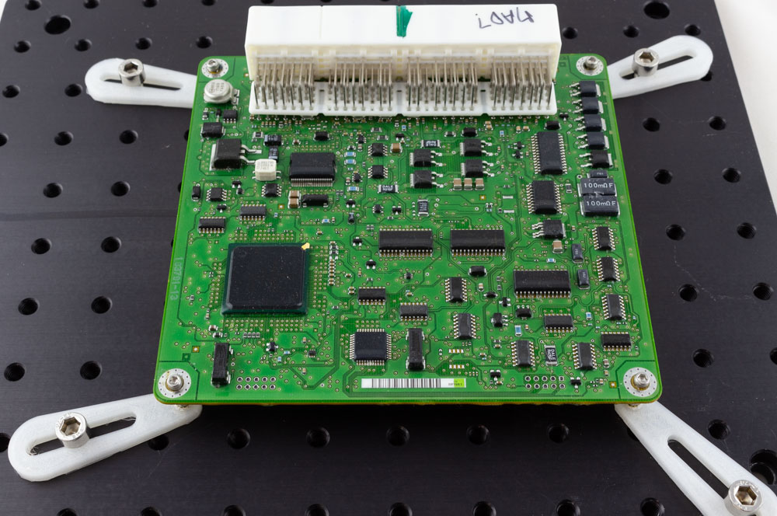
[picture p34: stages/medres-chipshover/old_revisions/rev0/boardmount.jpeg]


To set this up, simply:

1. Select a stand-off height as appropriate for your board. Typically the shortest stand-off possible provides the best mechanical stability.

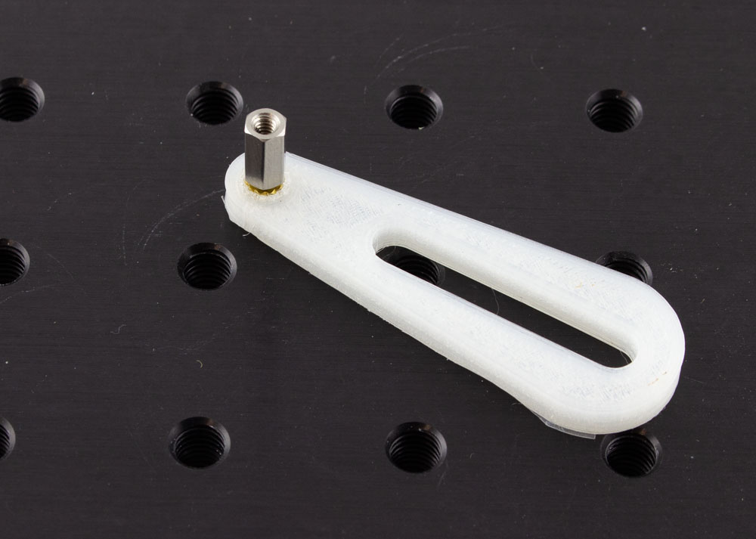
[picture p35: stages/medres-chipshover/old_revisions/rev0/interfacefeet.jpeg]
	

2. Roughly position the board and base pieces.

3. Loosely insert the M6 bolts & 4-40 bolts.

4. Tighten all bolts, performing final adjustments as needed before final tightening.

Be sure to consider the movement of the XY table and where your actual chip of interest is located. You can normally mount the board to provide some additional "coarse" adjustment range which makes for more rapid setup.

NOTE: We use a 4-40 thread in these plates as 4-40 bolt has a 2.85mm diameter. Thus a 4-40 bolt will always allow you to mount a board expecting a M3 bolt, as the 4-40 bolt has a slightly smaller diameter.

### Other Mounting Hardware

The base plate uses standard M6 threaded holes on a 25 x 25mm pattern. This allows usage of almost any optical mounts to help with your board mounting solutions.

In particular [Thor Labs](https://www.thorlabs.com/navigation.cfm?guide_id=2065) has a variety of mounts which you may find useful.

The metric [Pillar Post System](https://www.thorlabs.com/newgrouppage9.cfm?objectgroup_id=1316) provides a similar (but more rigid) solution to our board mounting kit. Note this uses a M6 bolt on top of the pillar - you likely will want to order a quantity of [M6 external to M3 internal adapters](https://www.thorlabs.com/thorproduct.cfm?partnumber=MSA6/M#ad-image-0). You can use this with M3 standoffs to easily mount boards to your table, or even [M3 to 4-40 adapters](https://www.mcmaster.com/91648A109/) if you need smaller screw holes.

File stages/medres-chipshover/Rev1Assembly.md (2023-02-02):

# Medium Res Stage - Rev 1 Assembly

NOTE: Due to use of US-centric parts (1" extrusion rails), some parts in this assembly are imperial screws/bolts.

As much as possible, imperial bolts are stainless steel (silver colour), and metric bolts are black.

## 1. Place Stage Frame on Table & Mount Vertical Supports

Remove base table from box, place on table. Yellow end caps may be preinstalled on one side, if so that is the "front". To avoid damage in shipping, we normally don't install the yellow end caps.

Mount vertical rails to base table rails by feeding T-Nuts into extrusion slots. 

Keep the rear of the rail support flush with the rear of the table for now. Lightly tighten the T-nuts using a 3/16 hex wrench (the uprights will still be a bit "wobbly" for now).

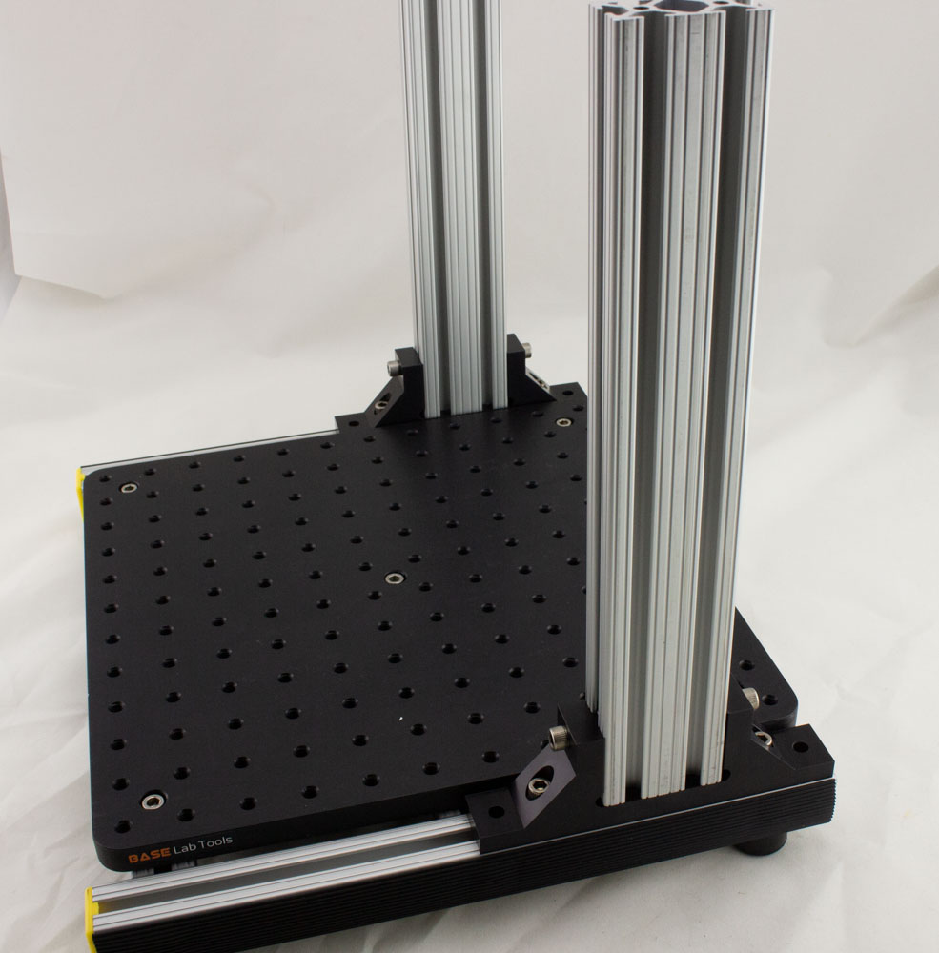
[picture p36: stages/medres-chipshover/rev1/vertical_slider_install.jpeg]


## 2. Mount Vertical Sliders with Upper Table (X Stage Support)

Slide the vertical table down the supports:

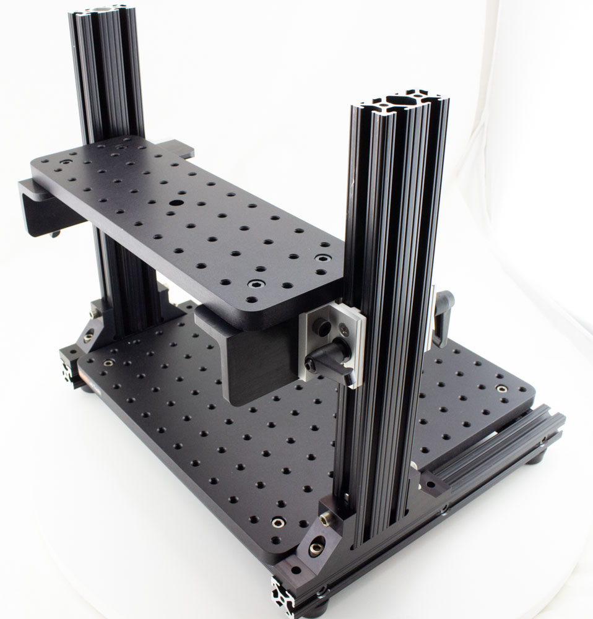
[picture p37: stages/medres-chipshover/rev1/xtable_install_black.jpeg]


To tighten the brakes on the slider, there are two L-handles on each side. To use them, you can turn them to tighten the brake. When you each the range of opening or closing, pull the handle out which disengages it from the bolt, allowing you to rotate it back:

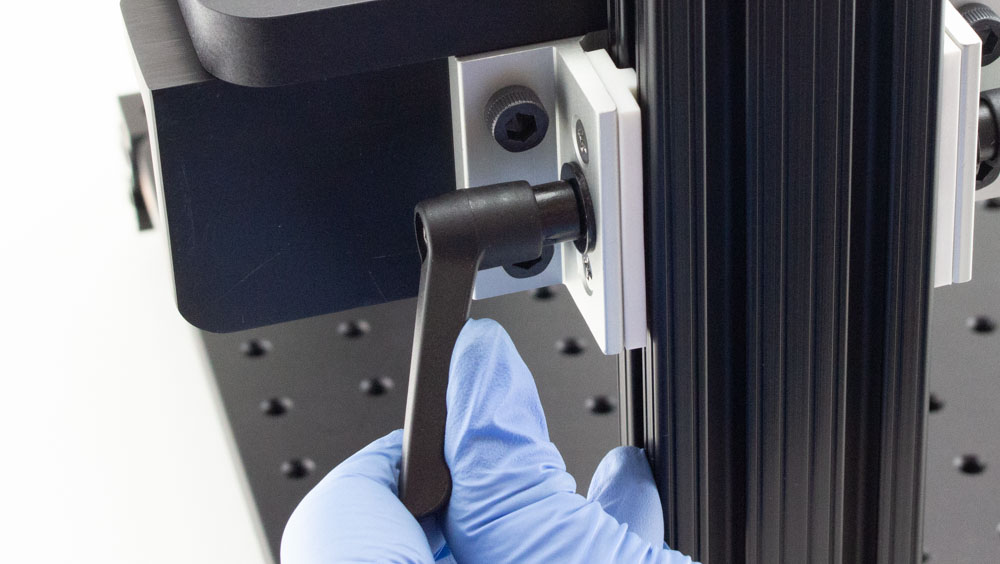
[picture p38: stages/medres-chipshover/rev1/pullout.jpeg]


You might prefer to just use a 3mm wrench to tighten and loosen the brake, especially during setup:

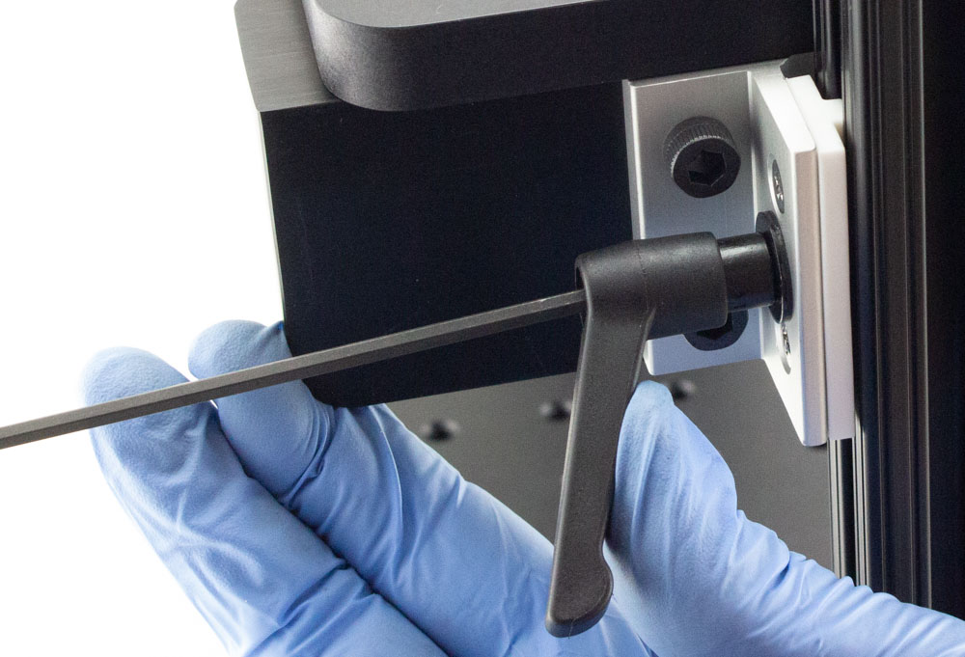
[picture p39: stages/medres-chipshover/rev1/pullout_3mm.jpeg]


When done, pull the handles out to disengage the brake, and move them out of the way so you don't hit them by accident:

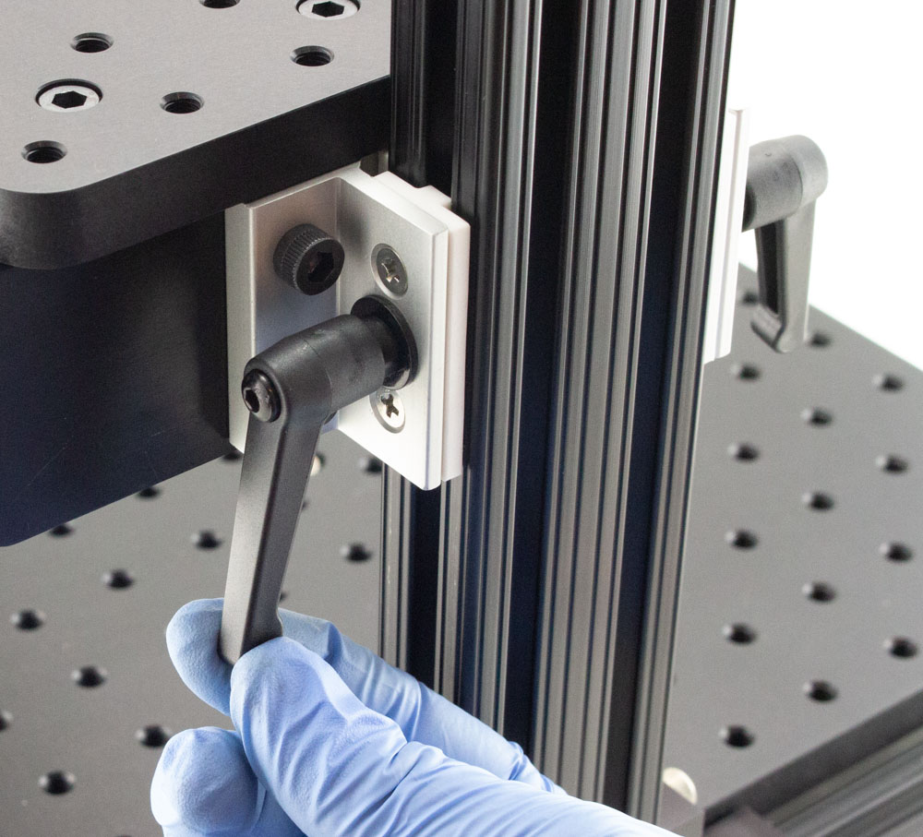
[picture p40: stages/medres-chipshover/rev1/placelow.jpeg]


## 3. Install X stage

You will need:

* 8: M6x14 bolts

Position X stage over support table - watch the alignment, as you need room for the DB9 cable to be mounted:

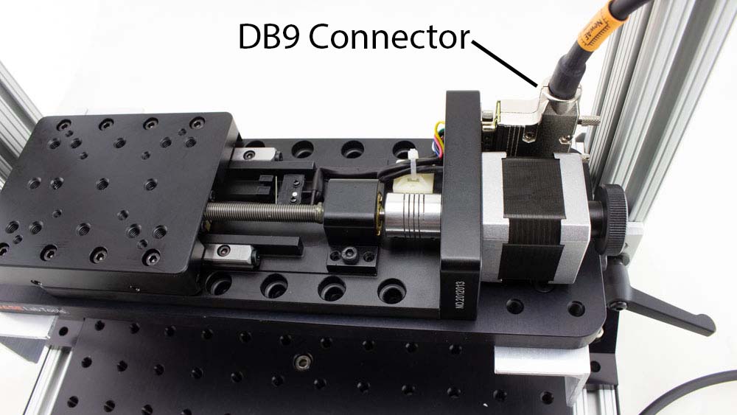
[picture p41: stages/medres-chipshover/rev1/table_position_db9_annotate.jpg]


Using the hand wheel, turn the table to expose the mounting holes. Then using 8 bolts, screw the X stage down
(8 bolts is excessive here probably, feel free to reduce this if you think you may adjust the position of the table):

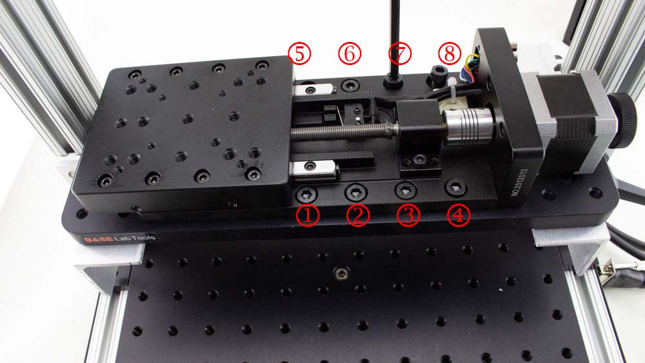
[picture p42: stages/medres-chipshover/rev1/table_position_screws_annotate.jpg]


## 4. Mount Y Axis Stage on X Axis

Mount the Y Axis stage perpendicular to the X axis stage. You will see alignment labels on the
X-axis stage that should align with the Y-axis stage. Note it will "overhang" the X axis stage to provide sufficient Y axis travel. The steps to perform the mounting are:

1. Using the handwheel, turn the Y axis stage until all **8** bolt-holes are visible underneath the Y axis stage (4 on each side). You will need to extend it almost to it's full limit for this.
2. Remove the 3x M6 bolts from the package.
3. Place the Y axis stage on the X axis stage - use alignment marks to position it, and keep one hand on the stage to avoid dropping it. Note that only **3** of the holes have matching threads.

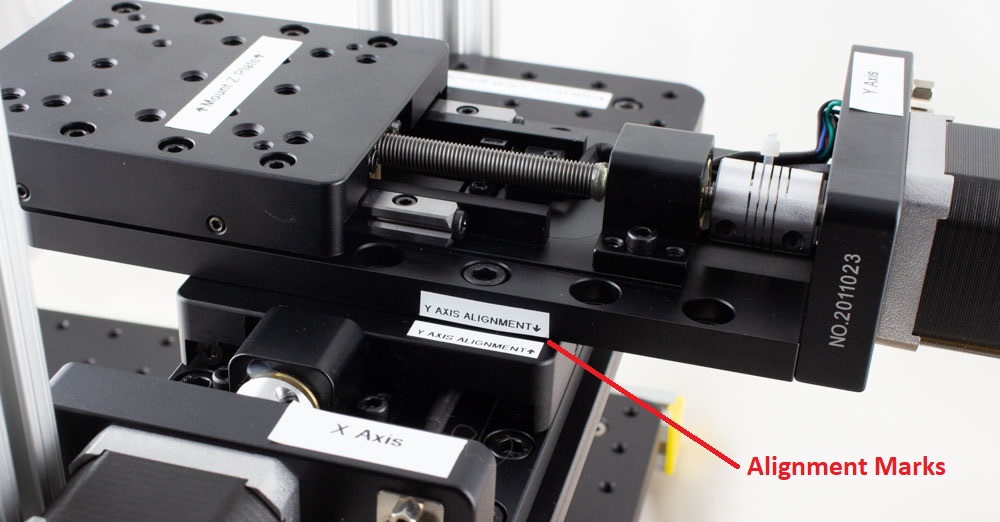
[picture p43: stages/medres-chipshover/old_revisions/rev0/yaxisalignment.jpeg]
	
4. Insert the M6 bolts, and using a 5mm hex driver tighten each bolt.

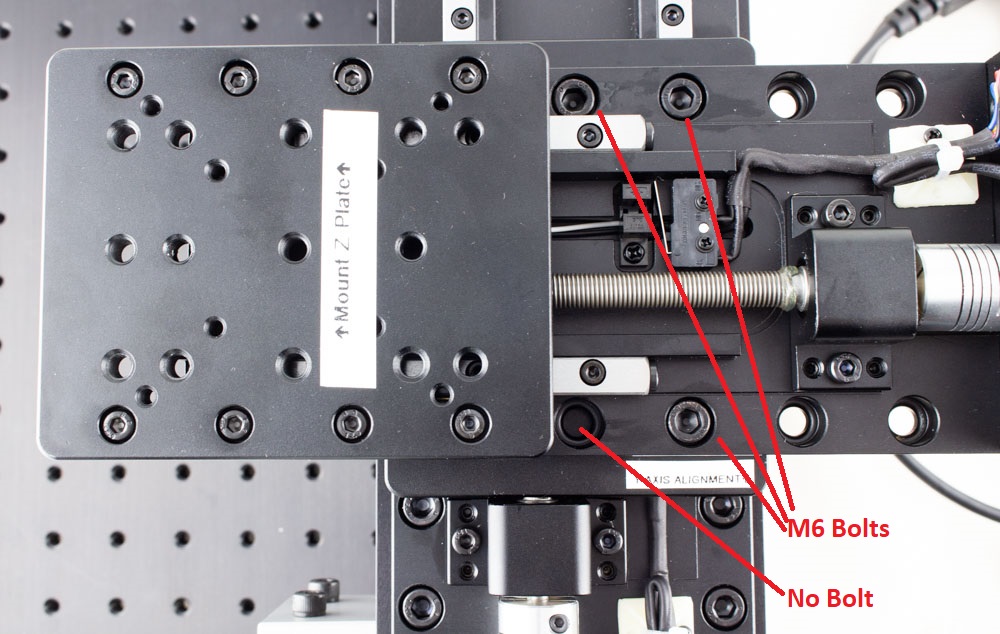
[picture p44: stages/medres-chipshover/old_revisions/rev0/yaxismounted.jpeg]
	
5. Using the Y axis handwheel, return the stage back to the "home" position (you'll hear the microswitch click). 

## 5. Mount Z Plate on Y Axis

**NOTE: This plate may be installed with the Z-Stage already, if so please follow this step, just hold the Z-Stage as well, and skip the next step as it's already done.**

1. Remove the 4x M6 bolts from the bag labelled "Z Plate to Y Axis Mounting Bolts".
2. Remove the Z plate from the packaging, and place on the Y axis stage.
3. Align the "Mount Z Plate" arrows, and insert the four bolts.

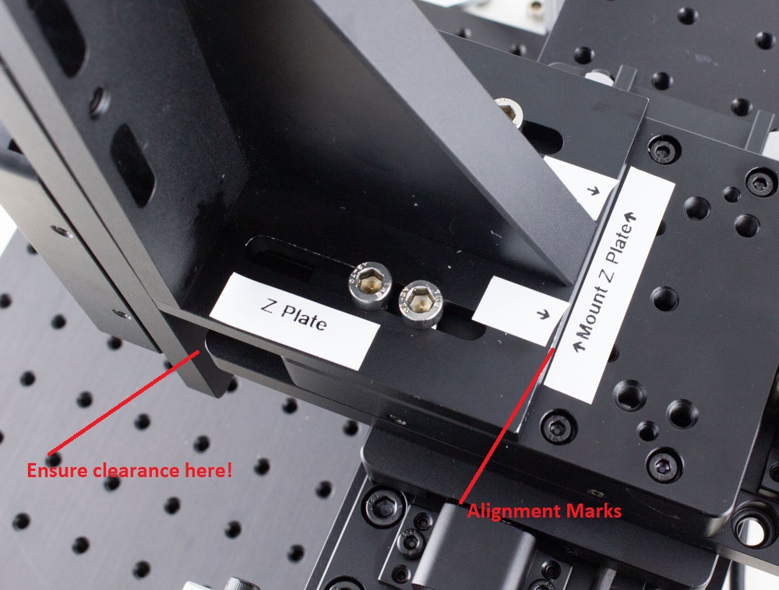
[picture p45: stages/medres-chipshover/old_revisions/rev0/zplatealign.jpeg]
	
4. Tighten the bolts - you'll have an ability to later fine-tune this mounting. You will want to make sure there is some clearance at the front of the Z axis mount when the Y axis is at the home position.

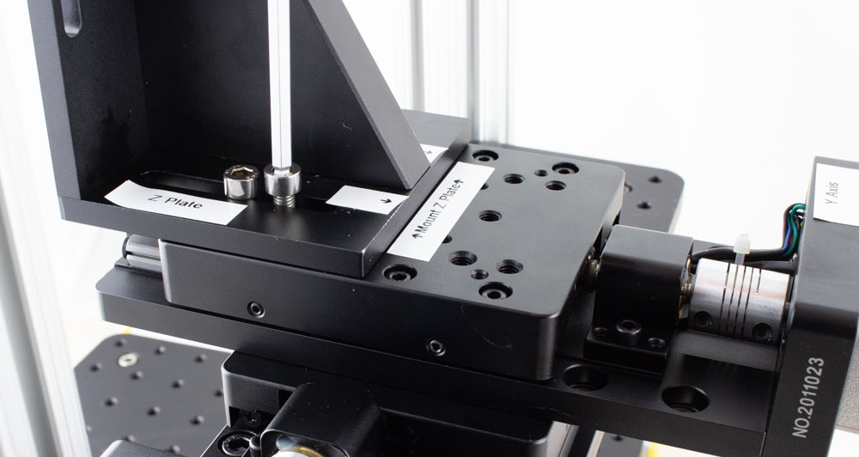
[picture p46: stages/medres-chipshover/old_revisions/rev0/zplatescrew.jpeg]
	

## 6. Mount Z Axis on Z Plate

You will be mounting the Z axis "lower" on the Z plate to provide a reasonable working distance for the ChipSHOUTER. The following photo shows where we will be mating the provided 2x M6 bolts - note we are *not* using the upper slot.

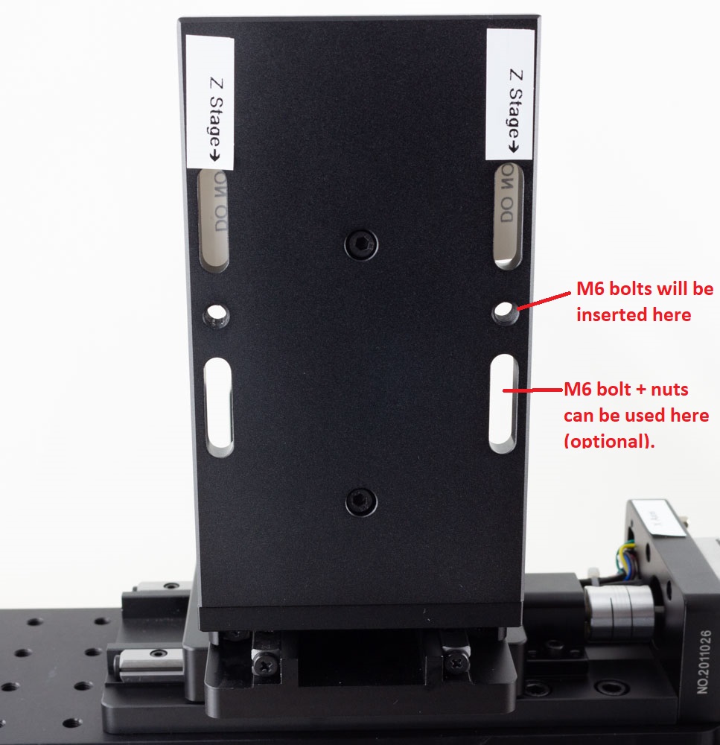
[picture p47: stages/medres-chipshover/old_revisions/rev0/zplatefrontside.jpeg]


1. Remove the 2x M6 bolts labelled "Z Axis to Z Plate Mounting Bolts"
2. Align the edge of the Z axis with the alignment marks on the Z plate.
3. Insert the 2x bolts that will mate into the threaded holes on the Z plate:

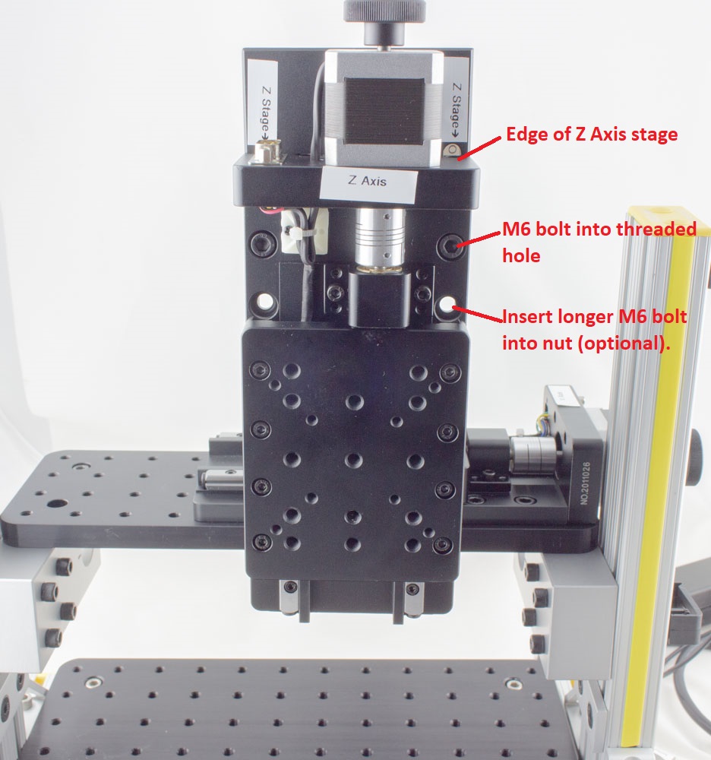
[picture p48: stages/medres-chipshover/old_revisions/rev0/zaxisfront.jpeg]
	
4. Optionally use the M6x20 bolts with the M6 locknuts.

HINT: You can adjust the position of the Z axis mounting for your own use, we simply provide a suggested mount location.

## 7. Adjustments & Locking Down

Check you have clearance at all limits - watch for example the far end of the X travel, where the Z plate may be close to the supports. You want at least 2-3mm of clearance here:

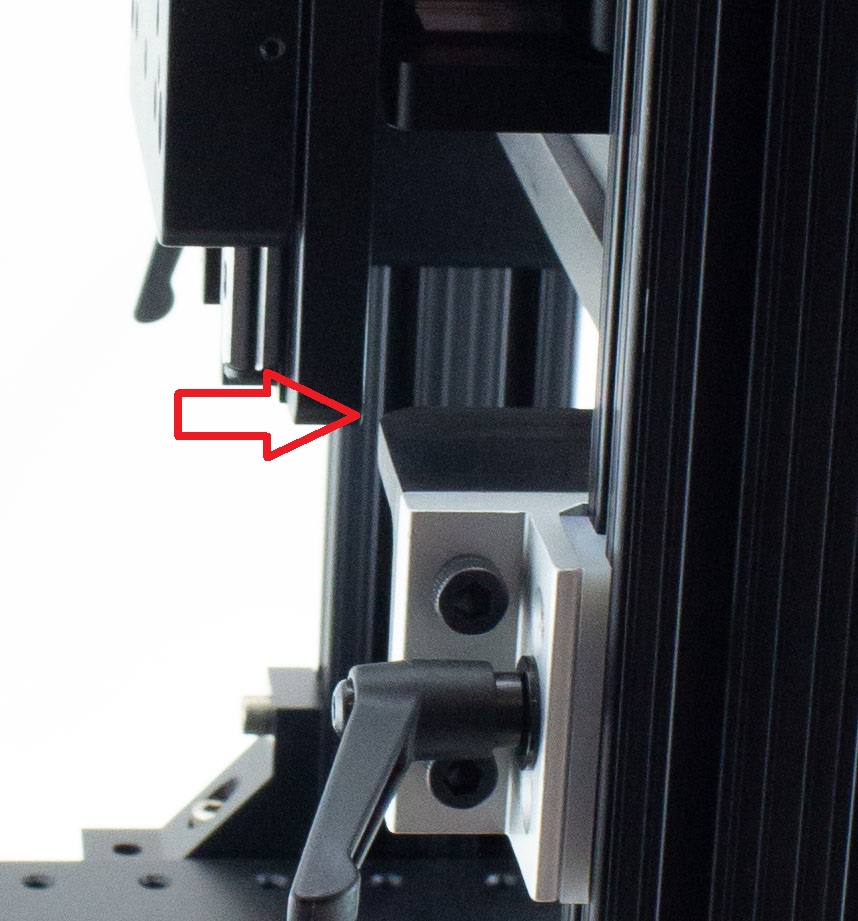
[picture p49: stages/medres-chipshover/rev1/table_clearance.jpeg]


You can adjust this by adjusting the Z-Plate mounting on the Y axis.

You can also adjust the small upper X-support table mount location, but this requires removing the X table (there upright-to-table-support angle pieces use slots allowing some adjustment). To do this, use a 10mm wrench on the flange nuts underneath the upright-to-table-supports.

If everything looks good, lock down the silver bolts you only loosely tightened in Step 1. They will bite into the rails for good rigidity, so this will feel tight. Use a 3/16" T-handle wrench (included).

You can also install yellow caps at this point to block the sharp edges of the extrusion:

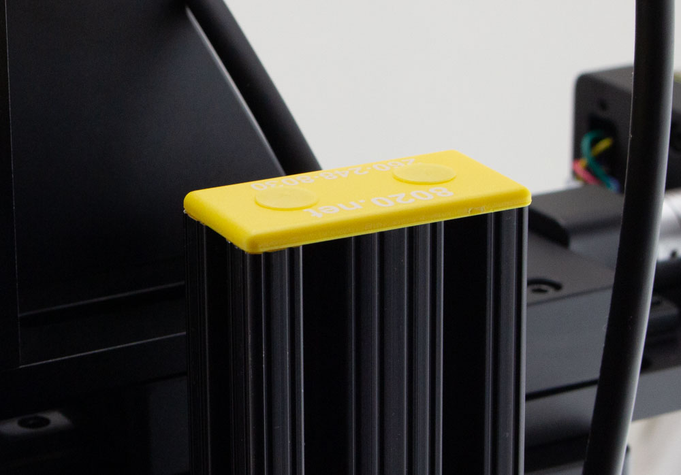
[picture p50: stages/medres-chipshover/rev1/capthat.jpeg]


## 8. Add Cable Mounts

You will use the Cable Mounts for routing stepper motor & ChipSHOUTER cables. The suggested uses is as shown here:

To insert them, simply insert into the slot and rotate the cable mounts (old revision shown for ChipShover):

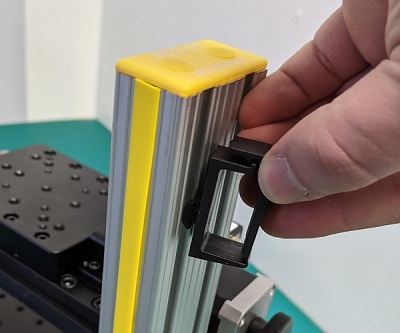
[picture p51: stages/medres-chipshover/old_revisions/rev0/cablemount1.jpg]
Insert & Rotate


To achieve the suggested mount locations, see this figure  (old revision shown for ChipShover):

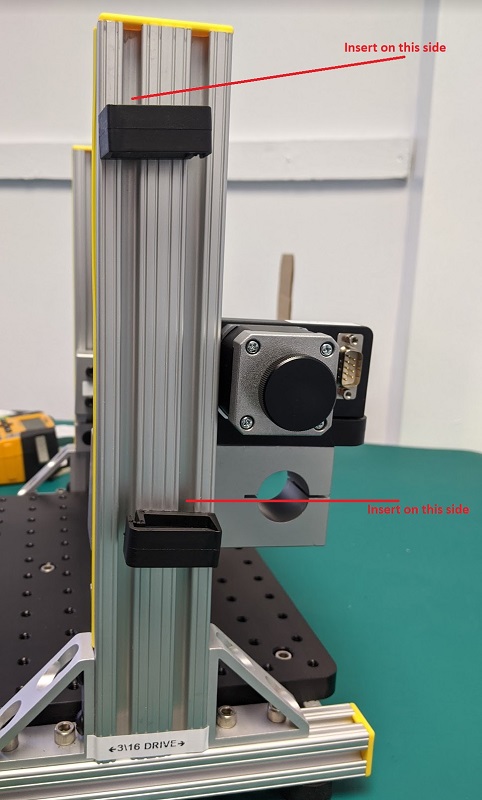
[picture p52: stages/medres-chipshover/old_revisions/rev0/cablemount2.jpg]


## 9. Connect Stepper Cables

The stepper motor cables are all standard DB-9 straight-through cables. The provided cables are 22AWG cables allowing a more powerful drive, although we have tested with standard 26AWG IDC cables successfully. Thus if you require extensions or replacements, and off the shelf cable should work.

Due to the spacing at the ChipShover controller the ChipShover mating side cannot use a backshell. Thus you may be limited to IDC style cables for off the shelf cables.

The X/Y/Z/ axis cables have been labelled to make setup quicker (the cables being electrically identical, but with different backshells to fit the stage orientation more cleanly). To connect them:

1. Connect each cable to the DB9 connector on each stage. The Z axis connector is straight up and the cable should be routed to a cable mount, the X and Y axis cables are right-angle and will route the cable downward (Y-axis) or upward (X-axis) as appropriate for the best install.
2. Tighten screws on the stage end connector.
3. Connect the other end of each cable to the ChipShover controller - the captive screws need to be tightened to mate the cables.

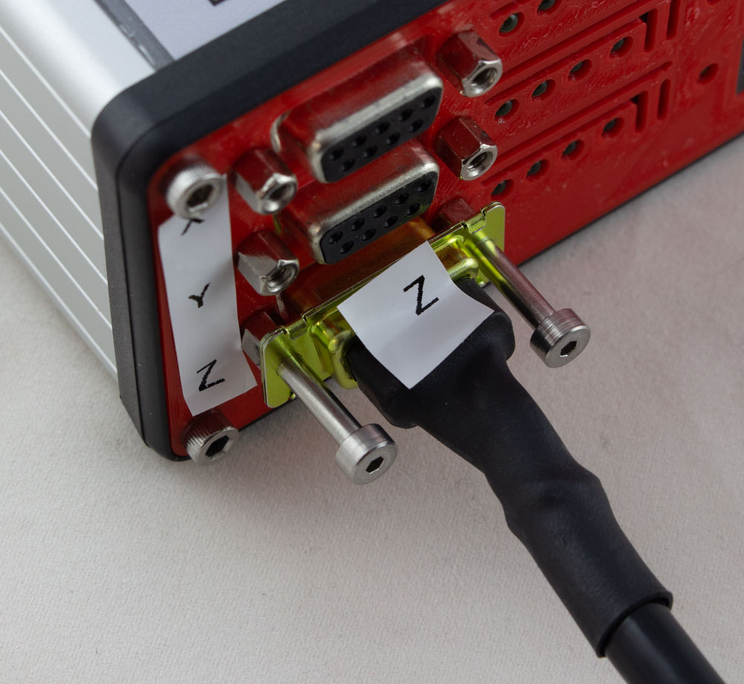
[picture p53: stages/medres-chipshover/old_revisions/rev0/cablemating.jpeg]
	

4. Route the cables through the ChipShover cable mounts as suitable (shown here also with ChipSHOUTER mounted - but note the Z stage cable routing through the lower mount).

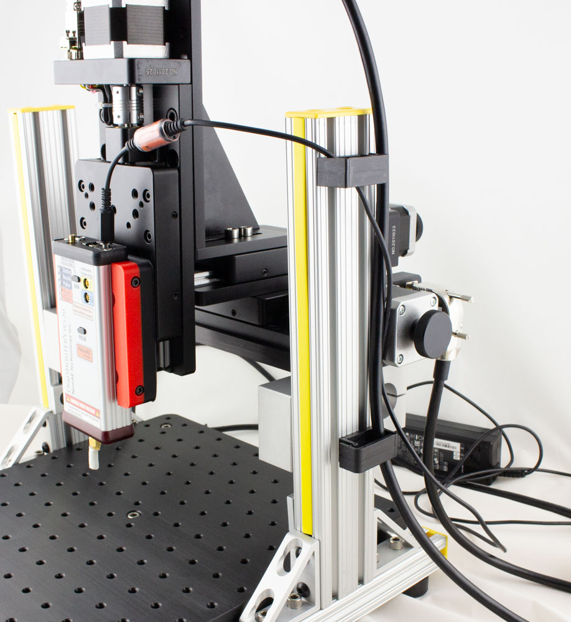
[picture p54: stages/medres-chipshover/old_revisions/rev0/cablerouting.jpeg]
	

	**HINT: If you you need to remove the captive screws from the cable on the ChipShover-One controller end, do this by holding the retaining washer with pliers and "backing out" the bolts.**

## 10. Optional - Test Table

At this point you can test the table before mounting the ChipSHOUTER. To test the table stand-alone:

1. Connect the power supply (4-pin mini-DIN).
2. Turn the power switch on - the switch should illuminate green. If the switch does not illuminate check the power supply.
3. The ChipShover should boot & display status information.
4. Release the E-Stop button by *Rotating it clockwise*, as the E-Stop may have been engaged during shipping.
5. Hold the "stop / home" button for 3-4 seconds - the ChipSHOVER should start the homing operation. You can release the button once it starts the homing operation.
6. **If the homing operation is failing (such as not detecting end-stops) press the E-Stop button immediately**.
7. Press the "Jog En" button to enable the joystick. You will see the Jog En light turn on.
8. Move the joystick in X & Y, and rotate it for Z. The current firmware moves by a fixed amount for each time period (this interface will be adjusted in the future). You can also hit the 'Fast Jog' button which changes the step size.
9. Power off the ChipShover & complete the rest of the steps.

## 11. Add ChipSHOUTER Mounting Bracket

The ChipSHOUTER mounting bracket fits onto the Z axis stage. Typically it is mounted "low" on the Z stage, where only the upper 2 bolts are used which provides more clearance:



Be sure to check you have sufficient clearance for the power & other connectors on the top-side of the ChipSHOUTER. If the ChipSHOUTER is mounted too high, it will cause a collision with the ChipSHOUTER cables and top of the stage.

The beveled end of the mounting bracket faces up.

## 12. Mount ChipSHOUTER

To mount the ChipSHOUTER into the bracket, use the two sliders on the side of the ChipSHOUTER. They should be positioned such the stops in the bracket will prevent the ChipSHOUTER from falling too low:

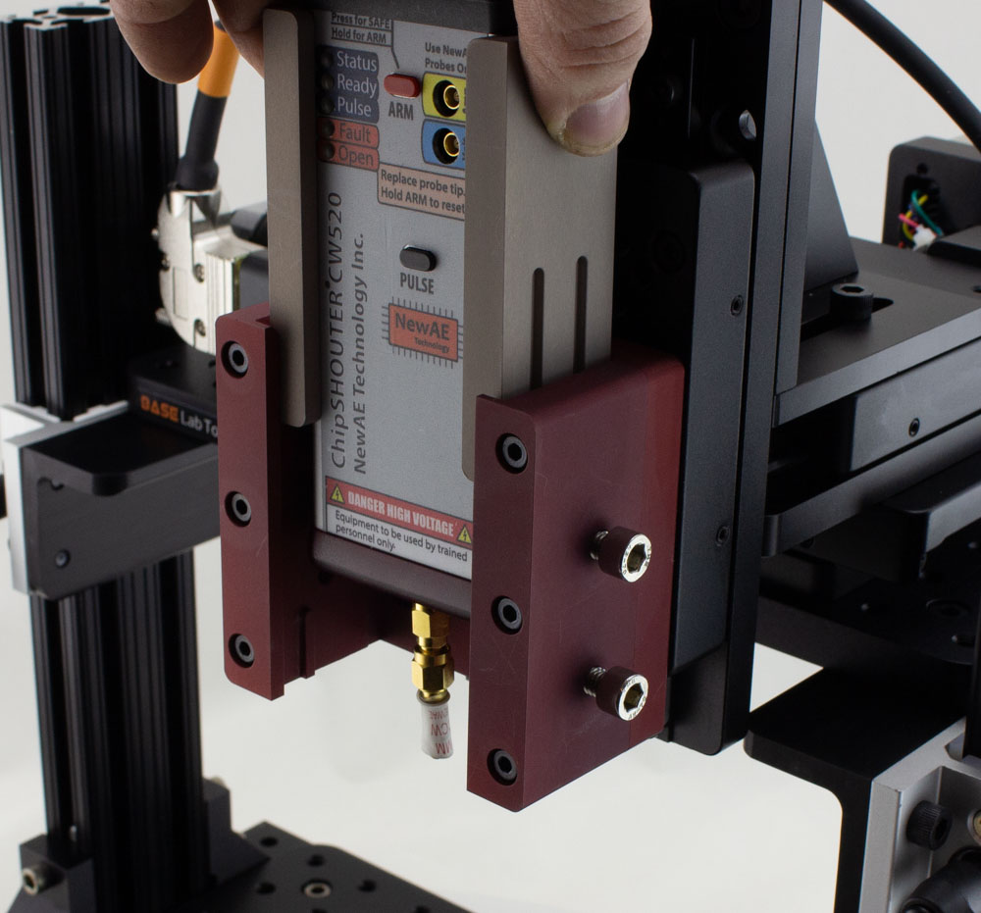
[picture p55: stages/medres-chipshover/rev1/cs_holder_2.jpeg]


To fix the position of the ChipSHOUTER, snug the bolts that hold the sliders in position **while holding the ChipSHOUTER and sliders from below**:

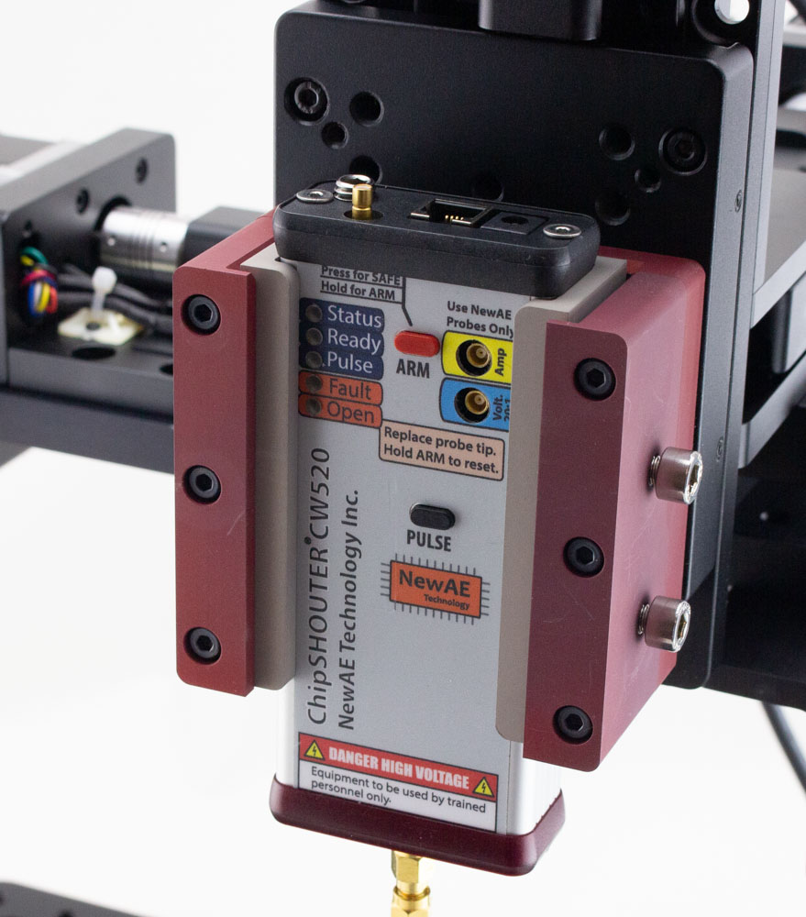
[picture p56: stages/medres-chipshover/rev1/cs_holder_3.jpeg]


Depending on your use-case, you might want to leave the bolts only tight enough to hold the bracket secure, but still loose enough such the ChipSHOUTER can slide if you accidentally drive it into your chip.

The bolt mounting allows you to quickly adjust the spacing of the ChipSHOUTER to compensate for various height boards you mount.

**NOTE:** You also may want the ChipSHOUTER at the "lower limit" of travel, such that it cannot drop any further. This prevents the ChipSHOUTER from dropping suddenly if the bolts loosen due to vibration of the table.

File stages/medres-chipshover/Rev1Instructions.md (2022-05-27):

# Medium Res Stage - Rev 1

REV1 is the initial release of the ChipShover platform. Updates will continue to be made to the platform.

## Stage Assembly & Setup

See the [Rev1Assembly.md](Rev1Assembly.md "Rev 1 Assembly Document") for details of the assembly process.

## ChipShover Python Interface

See [chipshover.readthedocs.io](https://chipshover.readthedocs.io/) for the full Python interface details.

## Adjusting Coarse Position

You will have to adjust the position of the ChipShover XYZ stages in a "coarse" fashion to get the ChipShover 50mm travel range to be within the area of your interest. 

### Y Adjustment

Loosen the two bolts along the Y sliders using a 3/16" hex, move to new position, tighten bolts.

### Z Adjustment

Holding the ChipShover upper table, release the four clamps. Adjust to the new position and tighten the clamps.

### Board Mounting Kit (PCB Paws)

We provide a board mounting kit, which consists of three pieces:

* Adjustable M6/slot to 4-40 base
* M6 mounting bolt
* 4-40 standoffs

This allows you to mount boards to the base, as in this example:



To set this up, simply:

1. Select a stand-off height as appropriate for your board. Typically the shortest stand-off possible provides the best mechanical stability.

	

2. Roughly position the board and base pieces.

3. Loosely insert the M6 bolts & 4-40 bolts.

4. Tighten all bolts, performing final adjustments as needed before final tightening.

Be sure to consider the movement of the XY table and where your actual chip of interest is located. You can normally mount the board to provide some additional "coarse" adjustment range which makes for more rapid setup.

NOTE: We use a 4-40 thread in these plates as 4-40 bolt has a 2.85mm diameter. Thus a 4-40 bolt will always allow you to mount a board expecting a M3 bolt, as the 4-40 bolt has a slightly smaller diameter.

### Other Mounting Hardware

The base plate uses standard M6 threaded holes on a 25 x 25mm pattern. This allows usage of almost any optical mounts to help with your board mounting solutions.

In particular [Thor Labs](https://www.thorlabs.com/navigation.cfm?guide_id=2065) has a variety of mounts which you may find useful.

The metric [Pillar Post System](https://www.thorlabs.com/newgrouppage9.cfm?objectgroup_id=1316) provides a similar (but more rigid) solution to our board mounting kit. Note this uses a M6 bolt on top of the pillar - you likely will want to order a quantity of [M6 external to M3 internal adapters](https://www.thorlabs.com/thorproduct.cfm?partnumber=MSA6/M#ad-image-0). You can use this with M3 standoffs to easily mount boards to your table, or even [M3 to 4-40 adapters](https://www.mcmaster.com/91648A109/) if you need smaller screw holes.

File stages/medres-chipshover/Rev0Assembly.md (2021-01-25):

# Medium Res Stage - Rev 0 Assembly

## Parts

Your shipment should contain the following boxes:

**Box 1: Frame with X Axis Stage**

 * Frame with X Axis already mounted
 * Extra-long 3/16" ball-end T-Handle driver
 * Extra-long 5/8" ball-end T-Handle driver
 * Box 6
 * Box 8

**Box 2: Y and Z Axis Stages**

* Y axis stage
* Y axis stage mounting bolts
* Z axis stage
* Z axis stage mounting bolts

**Box 3: Packing Box**

This was a numbering failure - ignore Box 3.

**Box 4 (inside Box 6): ChipSHOUTER Mount**

* ChipSHOUTER mounting adapter
* 4x M6 screws (countersunk)
* 4mm ball-end hex T-handle driver
* 4mm ball-end hex key

**Box 5 (inside Box 6): Mounting Hardware**

* 2x Cable Mounts for Frame
* DUT Mounts for Table:
	* Interface feet
	* 6x M6-10 bolts
	* 6x 4-40 x 1/4" standoff
	* 6x 4-40 x 3/8" standoff
	* 6x 4-40 x 3/4" standoff
	* 6x 4-40 x 1/4" cap head bolt
	* 6x 4-40 x 3/8" cap head bolt
* Misc hardware.

**Box 6 (inside Box 1): Z-Plate and Tools**

* Z Plate
* Z Plate screws
* 3/16" T Handle hex driver
* 5mm T Handle hex driver
* Flex-shaft driver
* Box 4
* Box 5

**Box 7: ChipShover Controller**

* ChipShover Controller
* Spare driver board
* Spare fuses

**Box 8 (inside Box 1): Stepper Cables**

* X axis stepper cable (1m)
* Y axis stepper cable (1m)
* Z axis stepper cable (1m)

## 1. Place Stage Frame on Table

Remove Box 6 & Box 8 from the box with the frame. Then you can remove the frame by holding the vertical framing members & pulling it up out of the box.

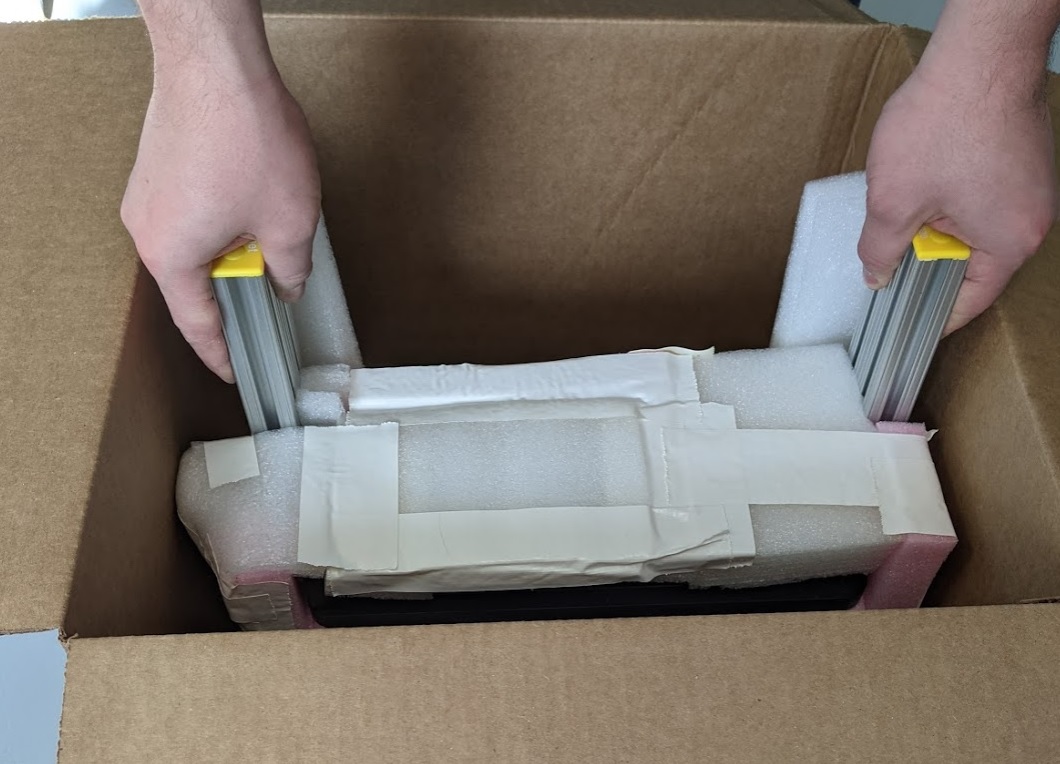
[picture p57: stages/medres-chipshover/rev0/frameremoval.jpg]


Remove packing material (foam & cardboard). Check the stage frame for any obvious damage.

## 2. Mount Y Axis Stage on X Axis

Mount the Y Axis stage perpendicular to the X axis stage. You will see alignment labels on the
X-axis stage that should align with the Y-axis stage. Note it will "overhang" the X axis stage to provide sufficient Y axis travel. The steps to perform the mounting are:

1. Using the handwheel, turn the Y axis stage until all **8** bolt-holes are visible underneath the Y axis stage (4 on each side). You will need to extend it almost to it's full limit for this.
2. Remove the 3x M6 bolts from the package.
3. Place the Y axis stage on the X axis stage - use alignment marks to position it, and keep one hand on the stage to avoid dropping it. Note that only **3** of the holes have matching threads.

	
4. Insert the M6 bolts, and using a 5mm hex driver tighten each bolt.

	
5. Using the Y axis handwheel, return the stage back to the "home" position (you'll hear the microswitch click). 

## 3. Mount Z Plate on Y Axis

1. Remove the 4x M6 bolts from the bag labelled "Z Plate to Y Axis Mounting Bolts".
2. Remove the Z plate from the packaging, and place on the Y axis stage.
3. Align the "Mount Z Plate" arrows, and insert the four bolts.

	
4. Tighten the bolts - you'll have an ability to later fine-tune this mounting. You will want to make sure there is some clearance at the front of the Z axis mount when the Y axis is at the home position.

	

## 4. Mount Z Axis on Z Plate

You will be mounting the Z axis "lower" on the Z plate to provide a reasonable working distance for the ChipSHOUTER. The following photo shows where we will be mating the provided 2x M6 bolts - note we are *not* using the upper slot.



1. Remove the 2x M6 bolts labelled "Z Axis to Z Plate Mounting Bolts"
2. Align the edge of the Z axis with the alignment marks on the Z plate.
3. Insert the 2x bolts that will mate into the threaded holes on the Z plate:

	
4. Optionally use the M6x20 bolts with the M6 locknuts.

HINT: You can adjust the position of the Z axis mounting for your own use, we simply provide a suggested mount location.

## 5. Add Cable Mounts

You will use the Cable Mounts for routing stepper motor & ChipSHOUTER cables. The suggested uses is as shown here:

To insert them, simply insert into the slot and rotate the cable mounts:

Insert & Rotate

To achieve the suggested mount locations, see this figure:



## 6. Connect Stepper Cables

The stepper motor cables are all standard DB-9 straight-through cables. The provided cables are 22AWG cables allowing a more powerful drive, although we have tested with standard 26AWG IDC cables successfully. Thus if you require extensions or replacements, and off the shelf cable should work.

Due to the spacing at the ChipShover controller the ChipShover mating side cannot use a backshell. Thus you may be limited to IDC style cables for off the shelf cables.

The X/Y/Z/ axis cables have been labelled to make setup quicker (the cables being electrically identical). To connect them:

1. Connect each cable to the DB9 connector on each stage. The Z axis connector is straight up and the cable should be routed to a cable mount, the X and Y axis cables are right-angle and will route the cable downward for a cleaner workspace.
2. Tighten screws on the stage end connector.
3. Connect the other end of each cable to the ChipShover controller - the captive screws need to be tightened to mate the cables.

	

4. Route the cables through the ChipShover cable mounts as suitable (shown here also with ChipSHOUTER mounted - but note the Z stage cable routing through the lower mount).

	

	**HINT: If you you need to remove the captive screws from the cable on the ChipShover-One controller end, do this by holding the retaining washer with pliers and "backing out" the bolts.**

## 7. Optional - Test Table

At this point you can test the table before mounting the ChipSHOUTER. To test the table stand-alone:

1. Connect the power supply (4-pin mini-DIN).
2. Turn the power switch on - the switch should illuminate green. If the switch does not illuminate check the power supply.
3. The ChipShover should boot & display status information.
4. Release the E-Stop button by *Rotating it clockwise*, as the E-Stop may have been engaged during shipping.
5. Hold the "stop / home" button for 3-4 seconds - the ChipSHOVER should start the homing operation. You can release the button once it starts the homing operation.
6. **If the homing operation is failing (such as not detecting end-stops) press the E-Stop button immediately**.
7. Press the "Jog En" button to enable the joystick.
8. Move the joystick in X & Y, and rotate it for Z. The current firmware moves by a fixed amount for each time period (this interface will be adjusted in the future).
9. Power off the ChipShover & complete the rest of the steps.

## 8. Add ChipSHOUTER Mounting Bracket

The ChipSHOUTER mounting bracket fits onto the Z axis stage. Typically it is mounted "low" on the Z stage, where only the upper 2 bolts are used:

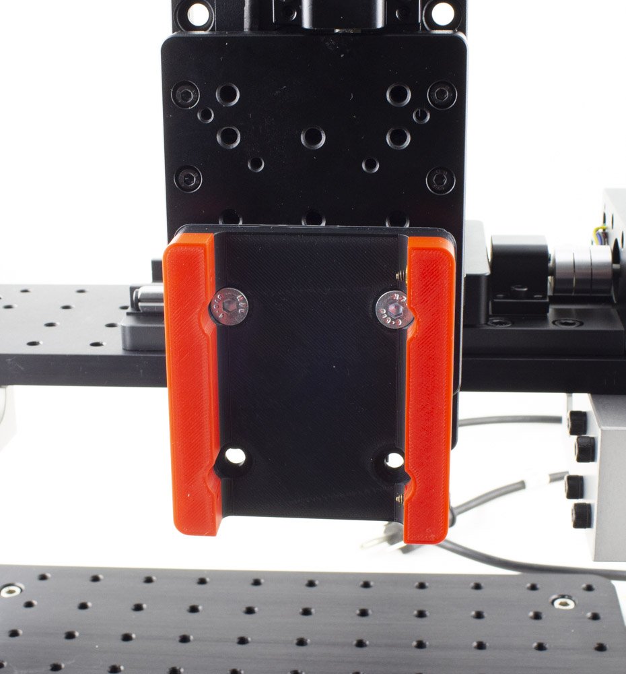
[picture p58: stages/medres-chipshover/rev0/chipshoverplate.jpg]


Be sure to check you have sufficient clearance for the power & other connectors on the top-side of the ChipSHOUTER. If the ChipSHOUTER is mounted too high, it will cause a collision with the ChipSHOUTER cables and top of the stage. See the example photos with the ChipSHOUTER present.

## 9. Mount ChipSHOUTER

To mount the ChipSHOUTER into the bracket, tighten the 6-32 socket head screws. These screws have a "soft brass" tip - they will still leave a small mark on the aluminum ChipSHOUTER enclosure, but the tip fit helps to secure the ChipSHOUTER into the bracket.

If you wish to avoid this mark, place a small piece of blanking metal (such as pop can metal) between the ChipSHOUTER enclosure and the screw tips. Be sure the screws are still sufficiently tight & will not loosen, we suggest using Loctite in them if you feel comfortable with the ChipSHOUTER configuration.

The 6-32 socket head screws use a 7/64" hex driver. This hex driver bit is included alongside the ChipSHOUTER mounting plate - you will need the flex driver to use this (you can use any other screwdriver as well with this).

Setup is now complete! Hopefully the end results look something like this:



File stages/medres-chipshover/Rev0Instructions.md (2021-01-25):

# Medium Res Stage - Rev 0

REV0 is a beta release of the ChipShover platform. This release includes:

* Temporary printed labels instead of final labels
* 3D printed parts

## Stage Assembly & Setup

See the [Rev0Assembly.md](Rev0Assembly.md "Rev 0 Assembly Document") for details of the assembly process.

You should roughly have the following after that page:



## ChipShover Python Interface

See [chipshover.readthedocs.io](https://chipshover.readthedocs.io/) for the full Python interface details.

## Adjusting Coarse Position

You will have to adjust the position of the ChipShover XYZ stages in a "coarse" fashion to get the ChipShover 50mm travel range to be within the area of your interest. 

To simplify the adjustment, you have been provided with two **extra-long** T-handle socket-end hex wrenches. One is 3/16", and one is 5/32".

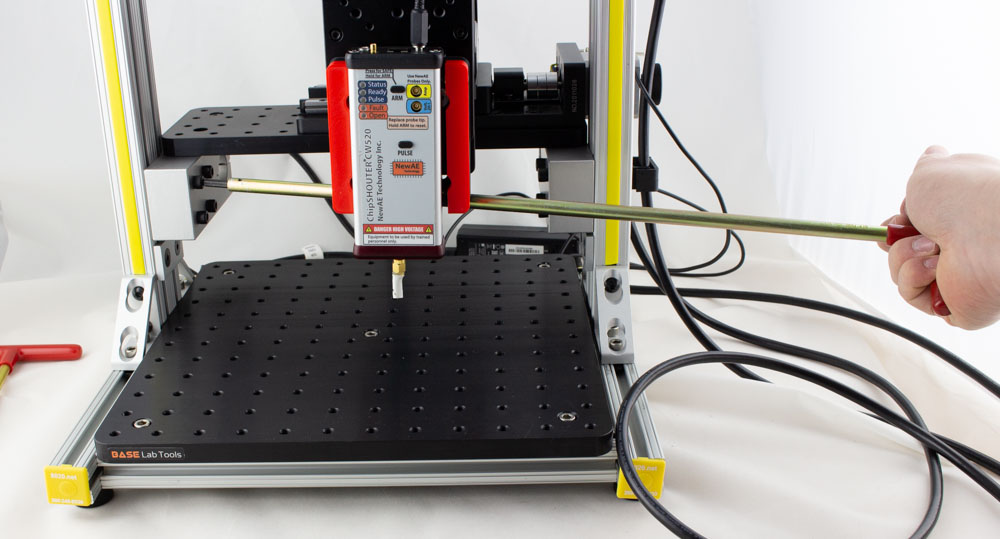
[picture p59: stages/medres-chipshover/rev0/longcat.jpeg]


The ChipShover table uses a "main adjustment bolt" that locks everything together - this bolt is the upper left bolt on the X-Axis table holder. Whenever you are moving the table either in Y or X you will have to loosen this bolt. Once you have finished the adjustment, tighten this bolt to ensure no other bolts loosen:

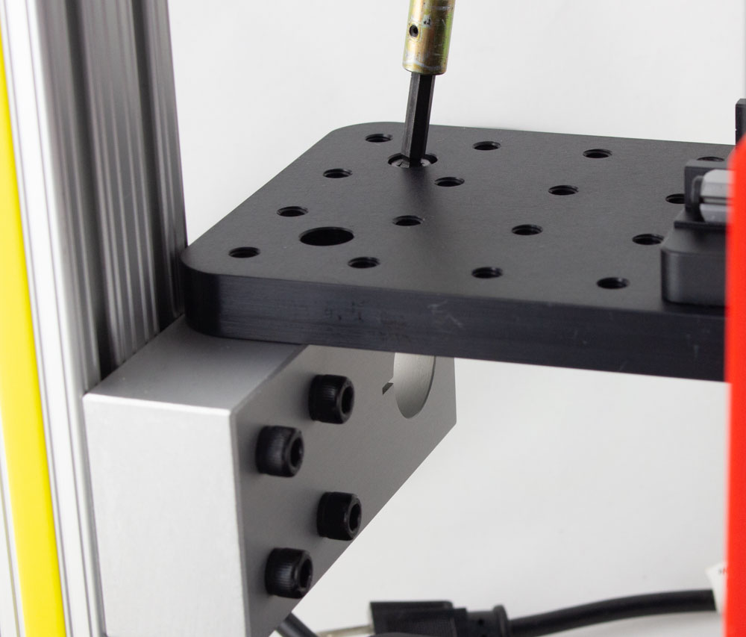
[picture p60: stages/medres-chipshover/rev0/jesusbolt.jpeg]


**NOTE: For all adjustments you should LOOSEN but not REMOVE any bolts. If you fully remove any bolt, be sure to thread them back before continuing.**

### Y Adjustment

1. Loosen the main adjustment bolt:

	

2. Loosen the **four** bolts on each side using a 3/16" hex wrench:

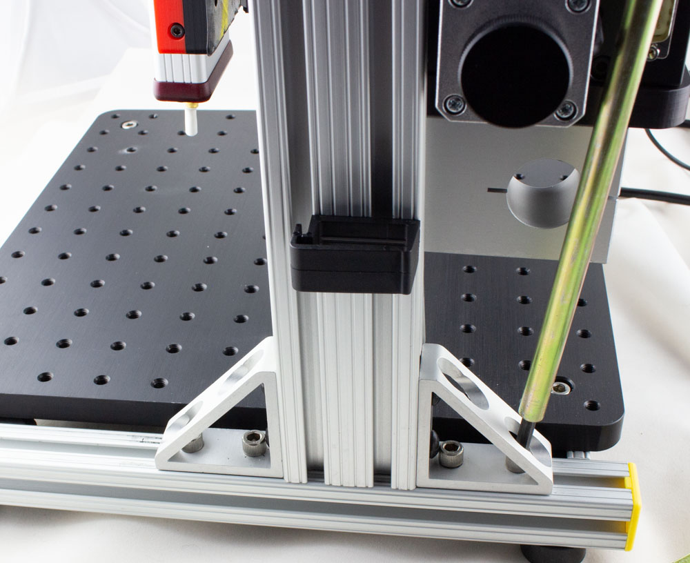
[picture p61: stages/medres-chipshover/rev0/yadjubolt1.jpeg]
	

   	**NOTE: One of the bolts will require you to access it at an angle - you may wish to only snug up this bolt to make adjustments easier**
	
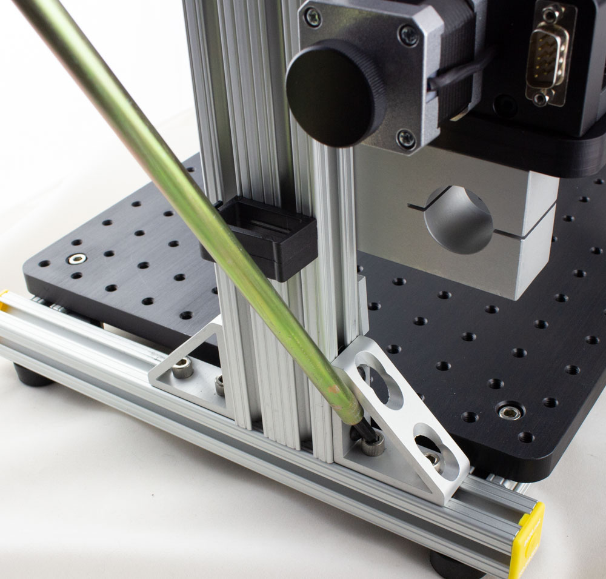
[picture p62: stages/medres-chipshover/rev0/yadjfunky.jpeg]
	

3. Pull the table to the new position:

	

4. Tighten the **four** bolts on each side using a 3/16" hex wrench:

	

5. Tighten the main adjustment bolt:

	

### Z Adjustment

**WARNING: When adjusting the Z axis, you may wish to remove the ChipSHOUTER mount. It is easy to knock the ChipSHOUTER during this operation which may damage it.**

#### Lowering

1. Using a 5/32" wrench, loosen the Z-stop bolts:

	

2. Set the new Z-stop location and tighten the bolts:

	

3.  Using a 3/16" hex wrench, loosen the four bolts underneath the X axis table on the left and right sides.

	

4. Loosen the main adjustment bolt, holding the table while doing so:

	

5. Gently lower the table onto the Z-axis stops:

	

6. Tighten the X axis table bolts - 4 on each side:

	

7. Tighten the main adjustment bolt:

	

Done!

#### Raising

1. Using a 3/16" hex wrench, loosen the four bolts underneath the X axis table on the left and right sides. Note there is a "stop" piece that will prevent any movement (dropping), you may wish to ensure these bolts are tight.

	

2. Loosen the main adjustment bolt:

	

3. Push up on both blocks to raise the table - you may need to *further* loosen some of the four bolts underneath each side from step 1 for this to work:

	

4. Keeping one hand on a block to "lock" it in place, tighten the main adjustment bolt. Note in the photo above you may find it handy to simply leave the provided shorter 3/16" wrench in the main bolt to make this easier:

	

5. Tighten the X axis table bolts - 4 on each side:

	

6. The Z-Stops are now too low - loosen the Z-stop bolt (using a 5/32" wrench):

	

7. Raise the Z-Stops and tighten them again:

	

Done!

## Mounting Boards to Base Plate

Typically you will need to mount various boards to the base plate for EMFI and SCA attacks.

### Board Mounting Kit

We provide a board mounting kit, which consists of three pieces:

* Adjustable M6/slot to 4-40 base
* M6 mounting bolt
* 4-40 standoffs

This allows you to mount boards to the base, as in this example:



To set this up, simply:

1. Select a stand-off height as appropriate for your board. Typically the shortest stand-off possible provides the best mechanical stability.

	

2. Roughly position the board and base pieces.

3. Loosely insert the M6 bolts & 4-40 bolts.

4. Tighten all bolts, performing final adjustments as needed before final tightening.

Be sure to consider the movement of the XY table and where your actual chip of interest is located. You can normally mount the board to provide some additional "coarse" adjustment range which makes for more rapid setup.

NOTE: We use a 4-40 thread in these plates as 4-40 bolt has a 2.85mm diameter. Thus a 4-40 bolt will always allow you to mount a board expecting a M3 bolt, as the 4-40 bolt has a slightly smaller diameter.

### Other Mounting Hardware

The base plate uses standard M6 threaded holes on a 25 x 25mm pattern. This allows usage of almost any optical mounts to help with your board mounting solutions.

In particular [Thor Labs](https://www.thorlabs.com/navigation.cfm?guide_id=2065) has a variety of mounts which you may find useful.

The metric [Pillar Post System](https://www.thorlabs.com/newgrouppage9.cfm?objectgroup_id=1316) provides a similar (but more rigid) solution to our board mounting kit. Note this uses a M6 bolt on top of the pillar - you likely will want to order a quantity of [M6 external to M3 internal adapters](https://www.thorlabs.com/thorproduct.cfm?partnumber=MSA6/M#ad-image-0). You can use this with M3 standoffs to easily mount boards to your table, or even [M3 to 4-40 adapters](https://www.mcmaster.com/91648A109/) if you need smaller screw holes.

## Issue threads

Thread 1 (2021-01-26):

ChipSHOUTER Mounting Bracket files are missing

colinoflynn, 2021-01-26:
The 3D printed mounting bracket files are missing (in case people want to 3D print them).

r0b0tsp1k3, 2022-12-03:
Please share these 3D files (STL) soon. The original bracket is hard to clip things onto so I want to "remix" the design: add attachment points to automatically switch to other tools such as chipjabber-basicbbi1 (please share the mounting bracket STL for that too).

colinoflynn, 2022-12-06:
Should be fixed now - version of it is at https://github.com/newaetech/ChipShover/tree/master/chipshouter_adapter/50mm_mounting_pattern/3dprinted_simple. We had a few variants that will try to upload (also added a newer version that was CNC machined as a reference).

colinoflynn, 2022-12-06:
Design was done in Fusion360, so have added those source files too (but the history of some of them is very messy, so the Fusion360 files may be less helpful than you hope for).

There was a variant that used the heat set inserts too, I'm checking if I've got the PN for the inserts and will upload that (otherwise it may be easier to modify the hole size to fit the insert you have).

Closed 2022-12-06.

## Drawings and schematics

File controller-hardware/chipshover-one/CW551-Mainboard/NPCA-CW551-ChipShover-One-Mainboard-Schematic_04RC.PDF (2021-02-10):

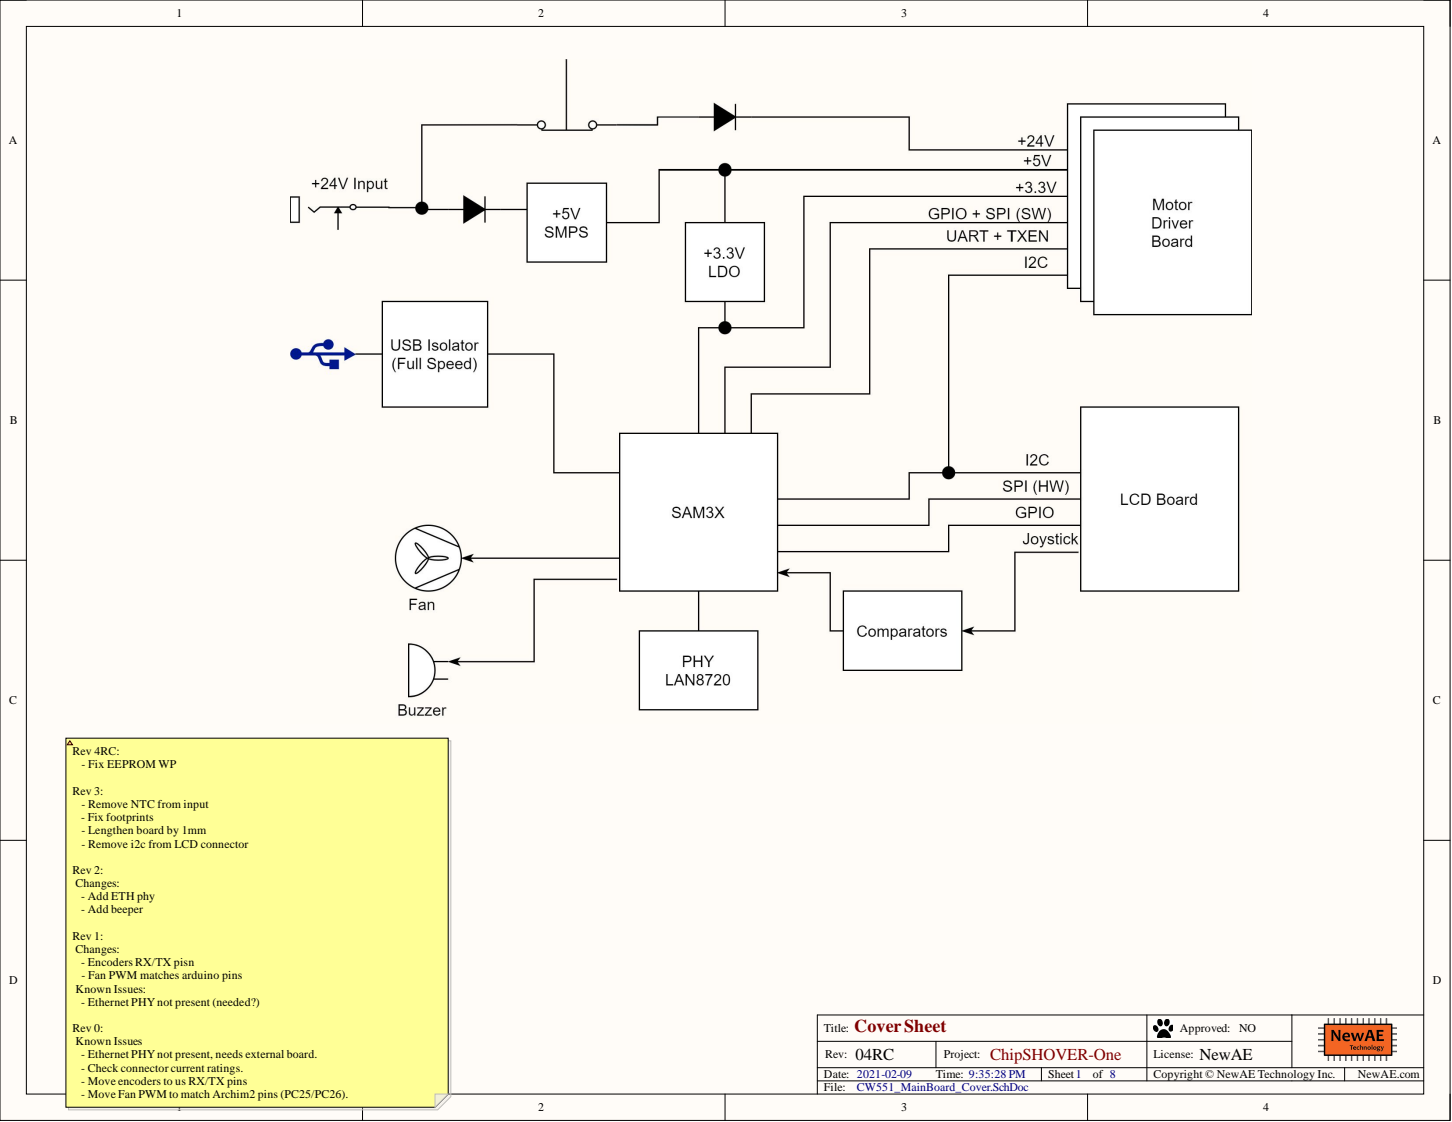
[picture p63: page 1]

Rev 3:
- Remove NTC from input
- Fix footprints
- Lengthen board by 1mm
- Remove i2c from LCD connector

Rev 1:
Changes:
- Encoders RX/TX pisn
- Fan PWM matches arduino pins
Known Issues:
- Ethernet PHY not present (needed?)

Rev 0:
Known Issues
- Ethernet PHY not present, needs external board.
- Check connector current ratings.
- Move encodersto us RX/TX pins
- Move Fan PWM to match Archim2 pins (PC25/PC26).

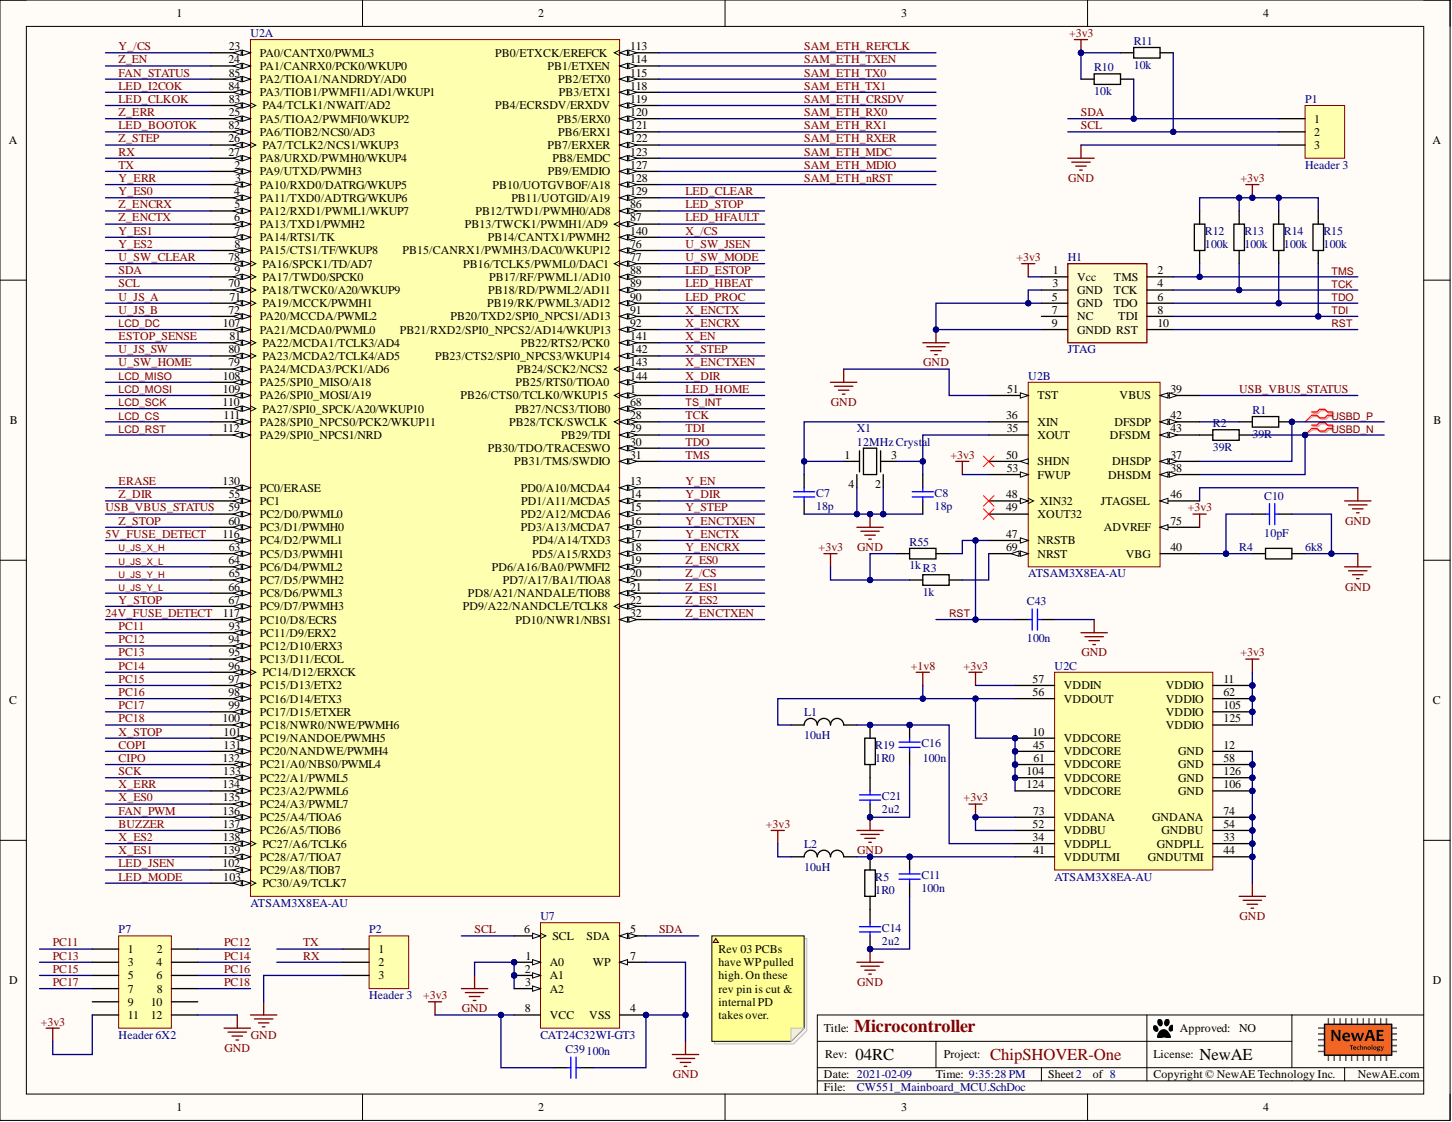
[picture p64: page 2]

TMS TDO TCK RST

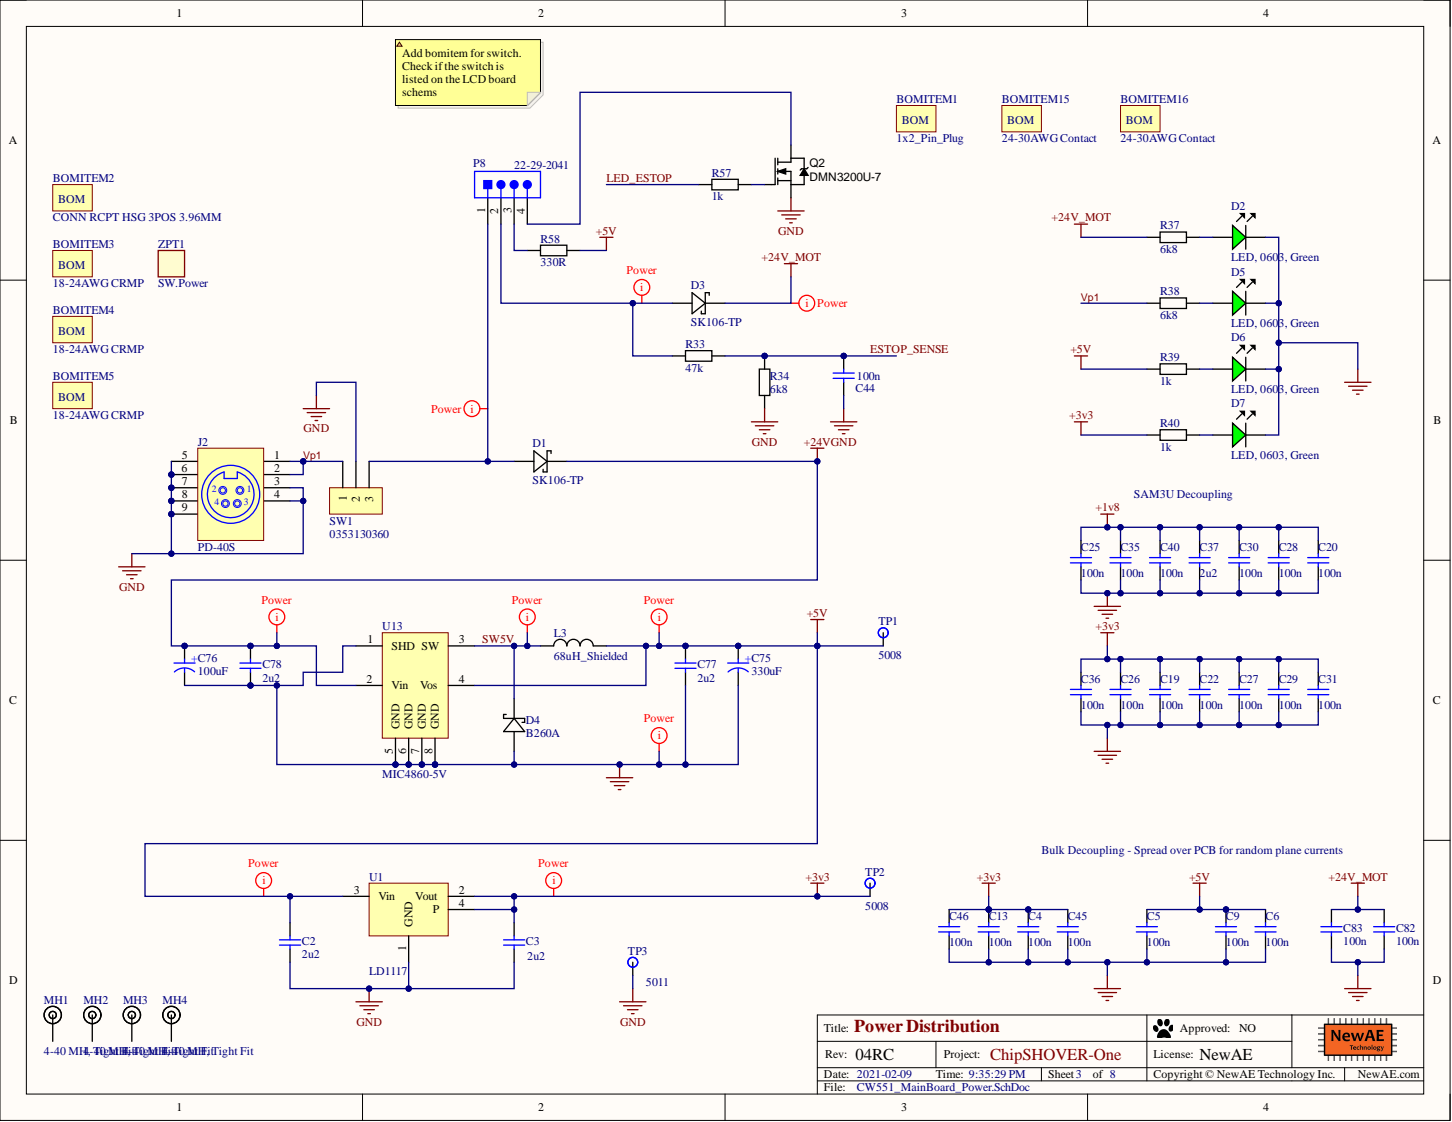
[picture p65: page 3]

Add bomitem for switch.
Check if the switch is
listed on the LCD board
schems

9 | 4 3

Vin 2 | 68uH_Shielded

Bulk Decoupling - Spread over PCB for random plane currents

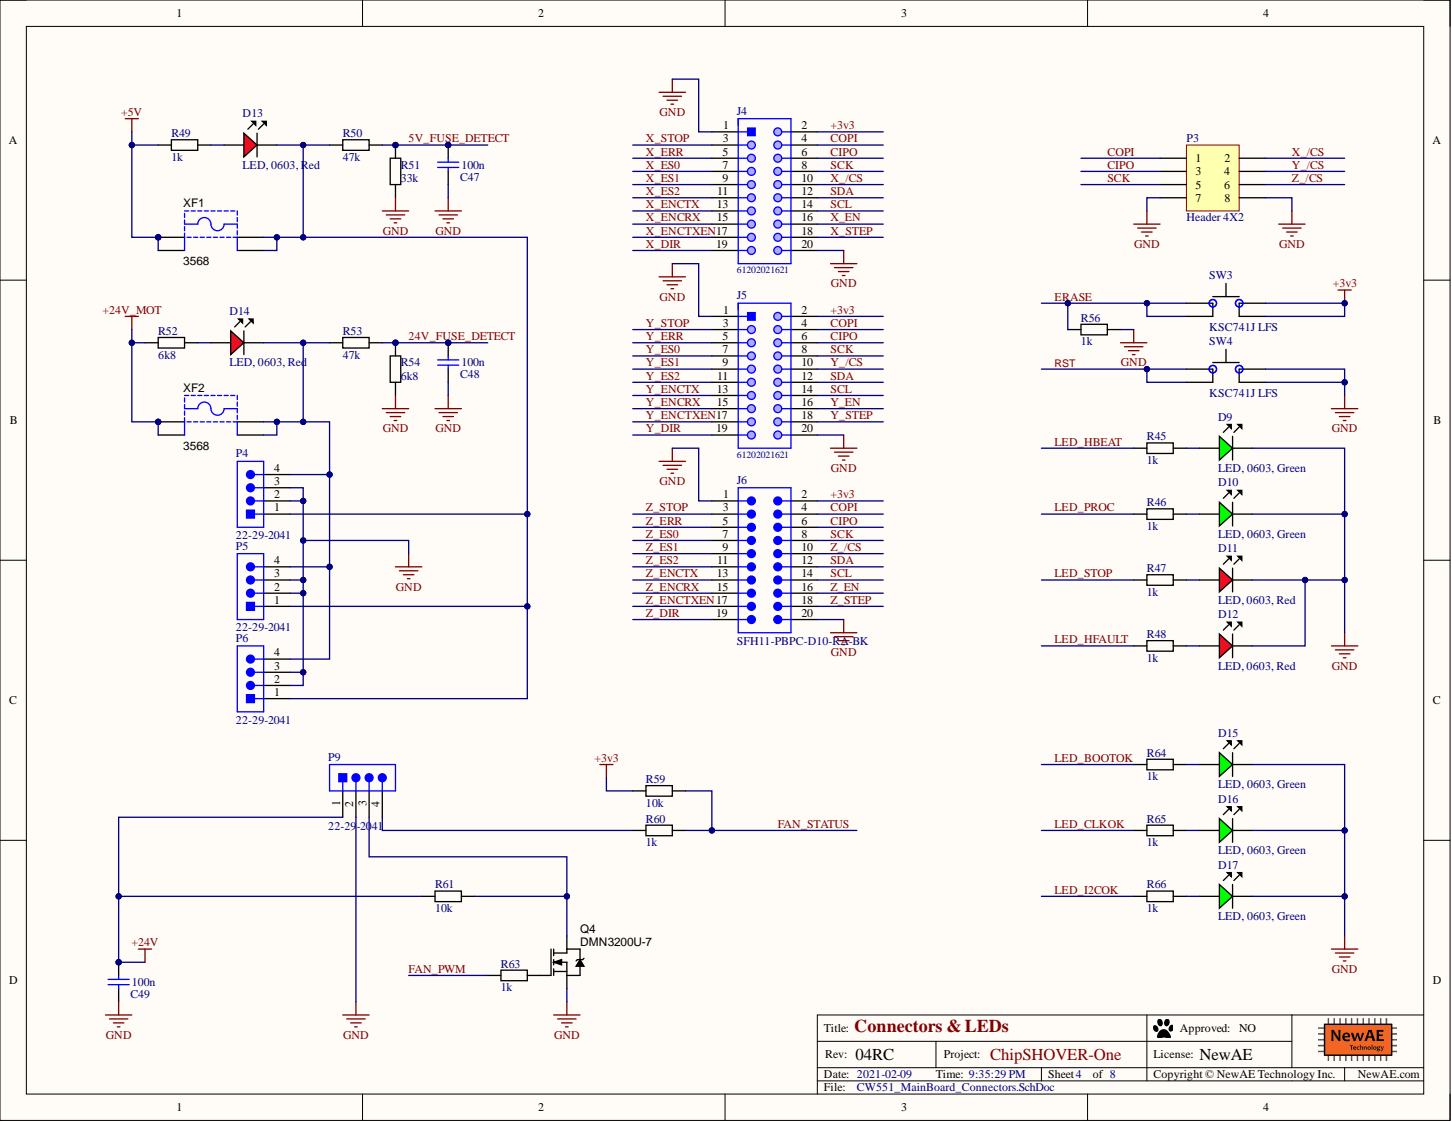
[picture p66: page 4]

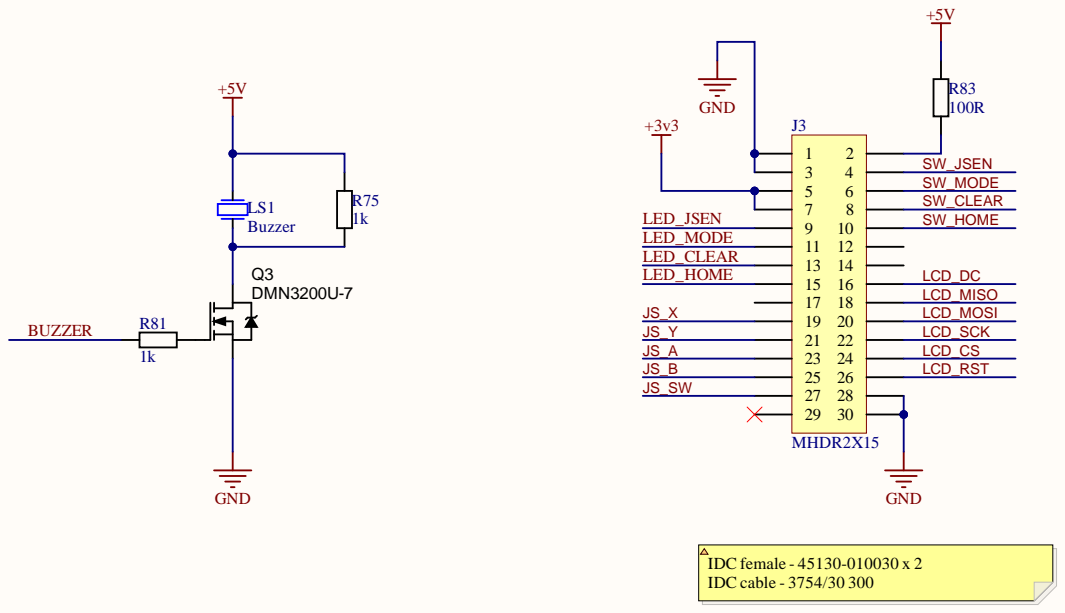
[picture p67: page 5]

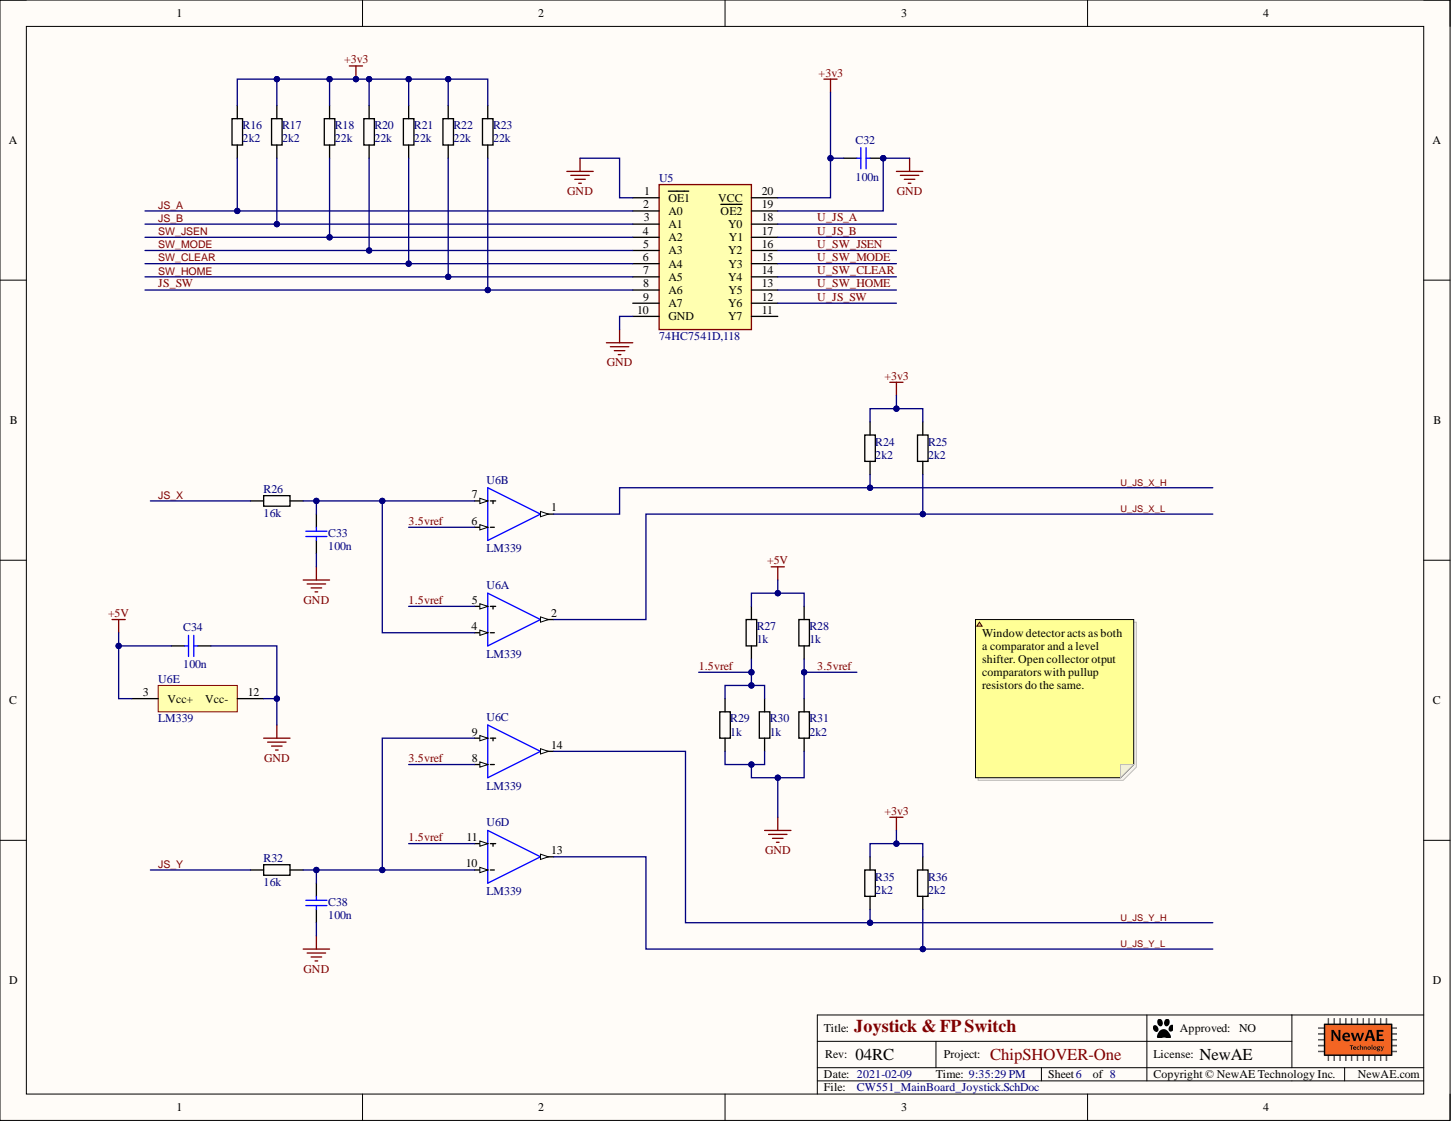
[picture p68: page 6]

Window detector acts as both
a comparator and a level
shifter. Open collector otput
comparators with pullup
resistors do the same.

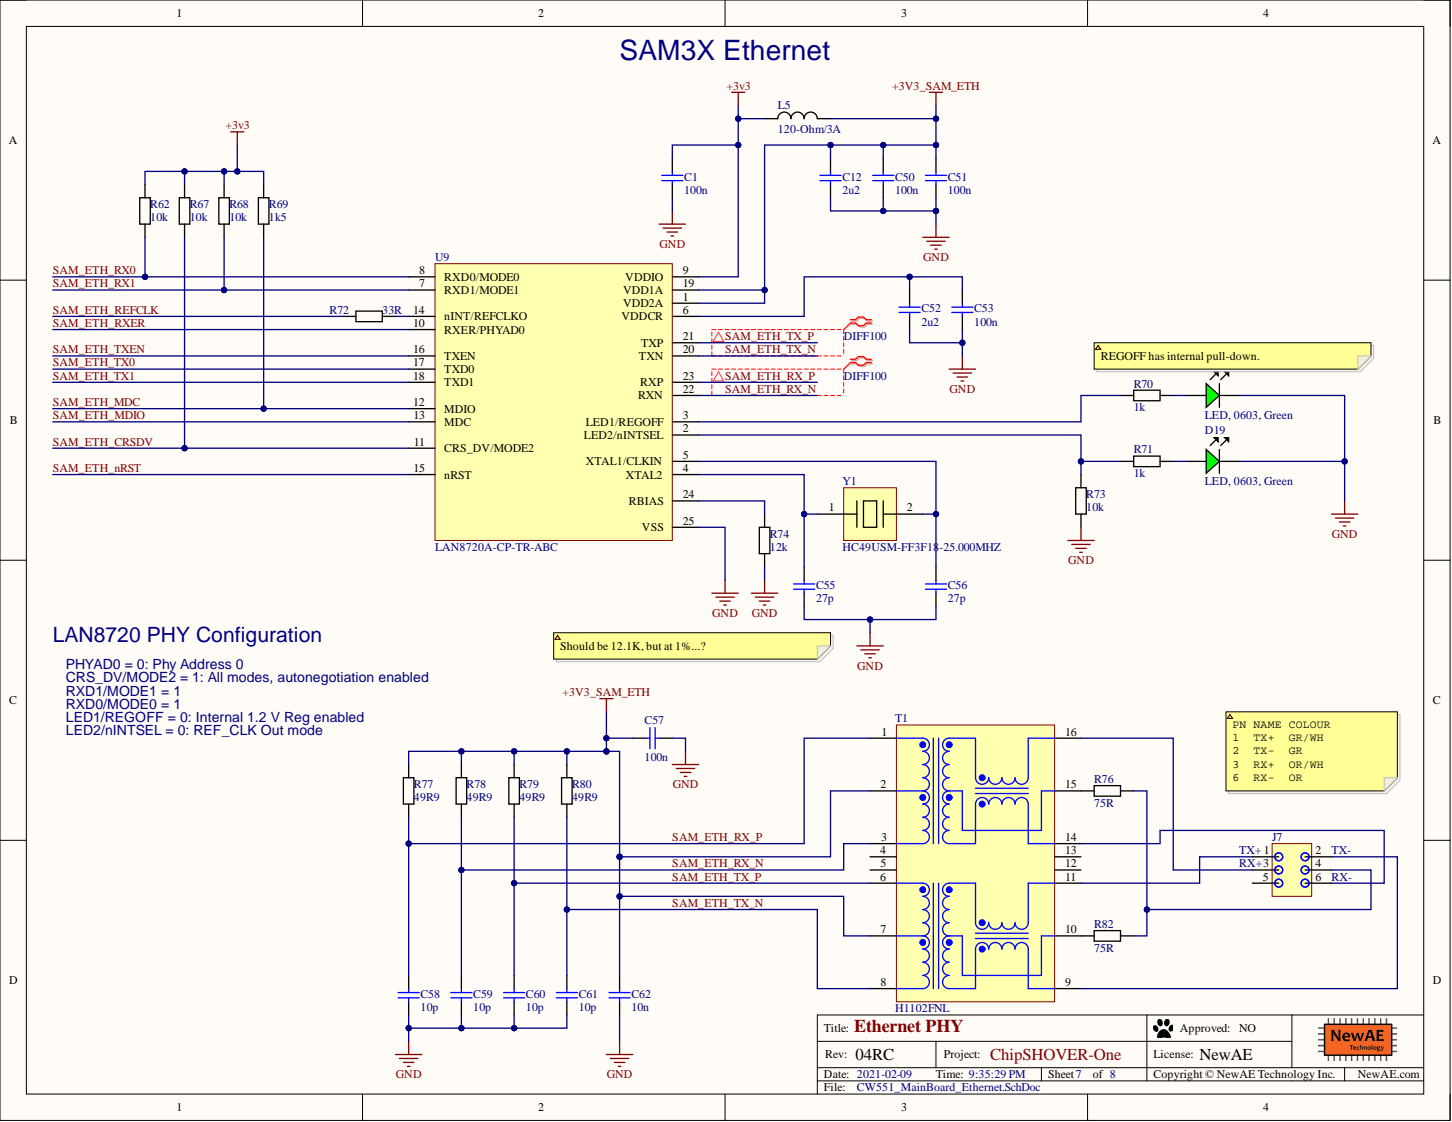
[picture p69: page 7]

REGOFF has internal pull-down.

Should be 12.1K, but at 1%...?

PHYAD0 = 0: Phy Address 0
CRS_DV/MODE2 = 1: All modes, autonegotiation enabled
RXD1/MODE1 = 1
RXD0/MODE0 = 1
LED1/REGOFF = 0: Internal 1.2 V Reg enabled
LED2/nINTSEL = 0: REF_CLK Out mode

SAM_ETH_RX_P

14
13

SAM_ETH_RX_N SAM_ETH_TX_P SAM_ETH_TX_N | 5 | | 12 | RX+ | 3 | 4

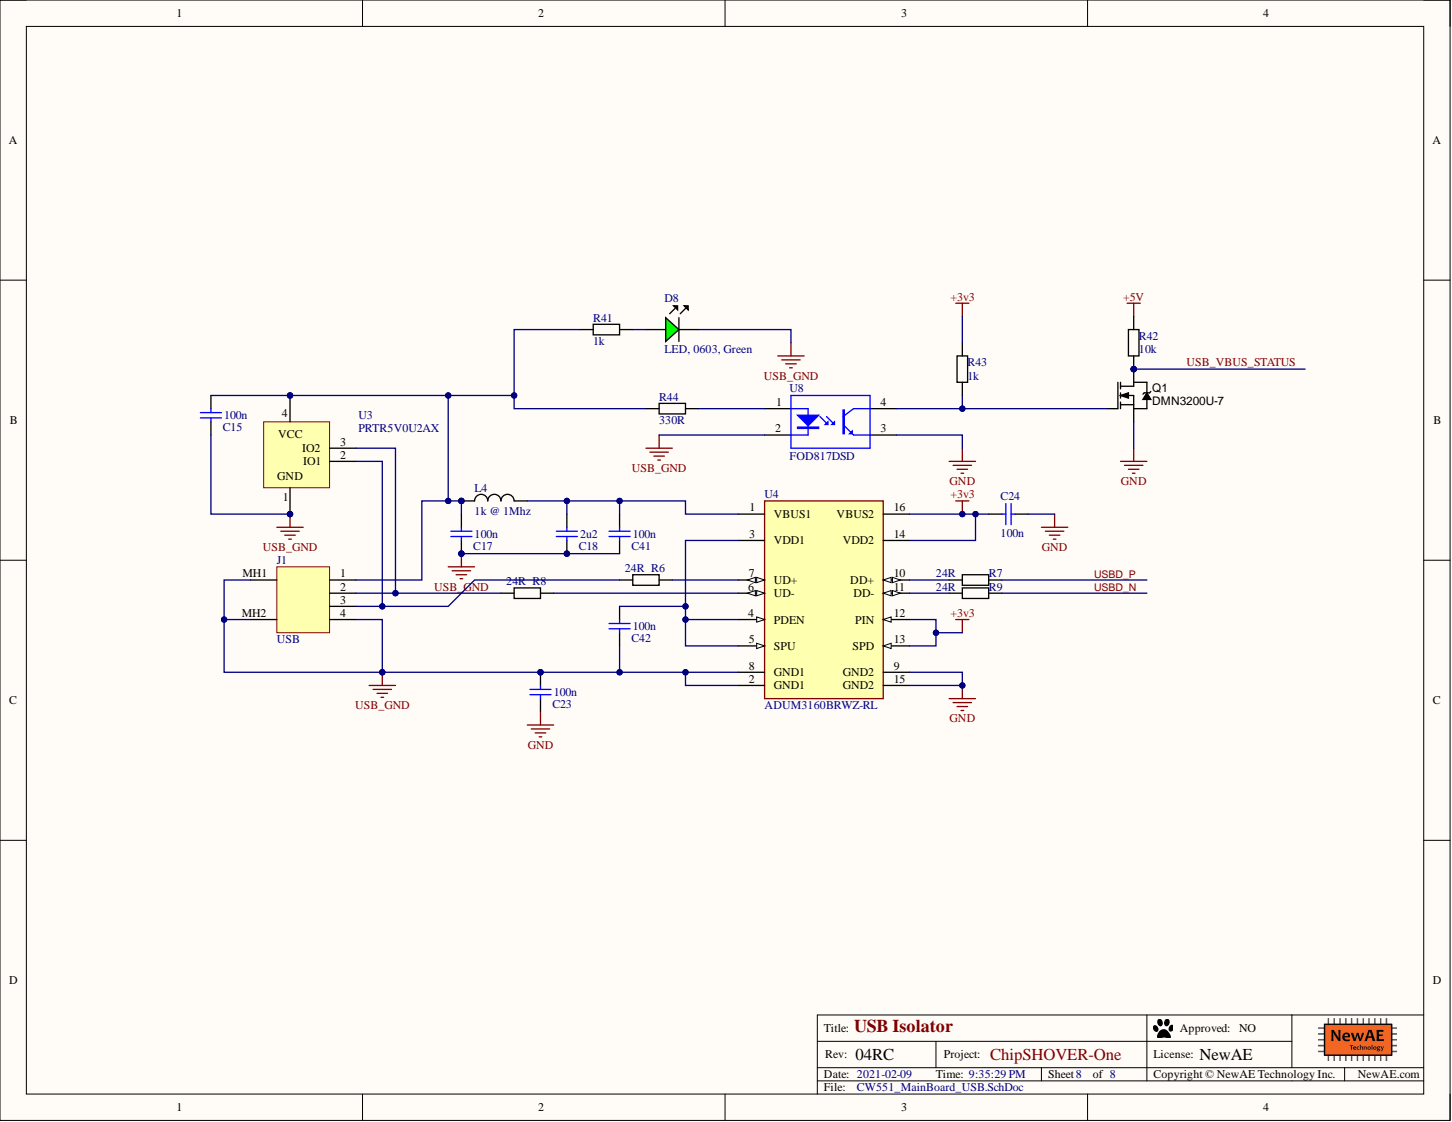
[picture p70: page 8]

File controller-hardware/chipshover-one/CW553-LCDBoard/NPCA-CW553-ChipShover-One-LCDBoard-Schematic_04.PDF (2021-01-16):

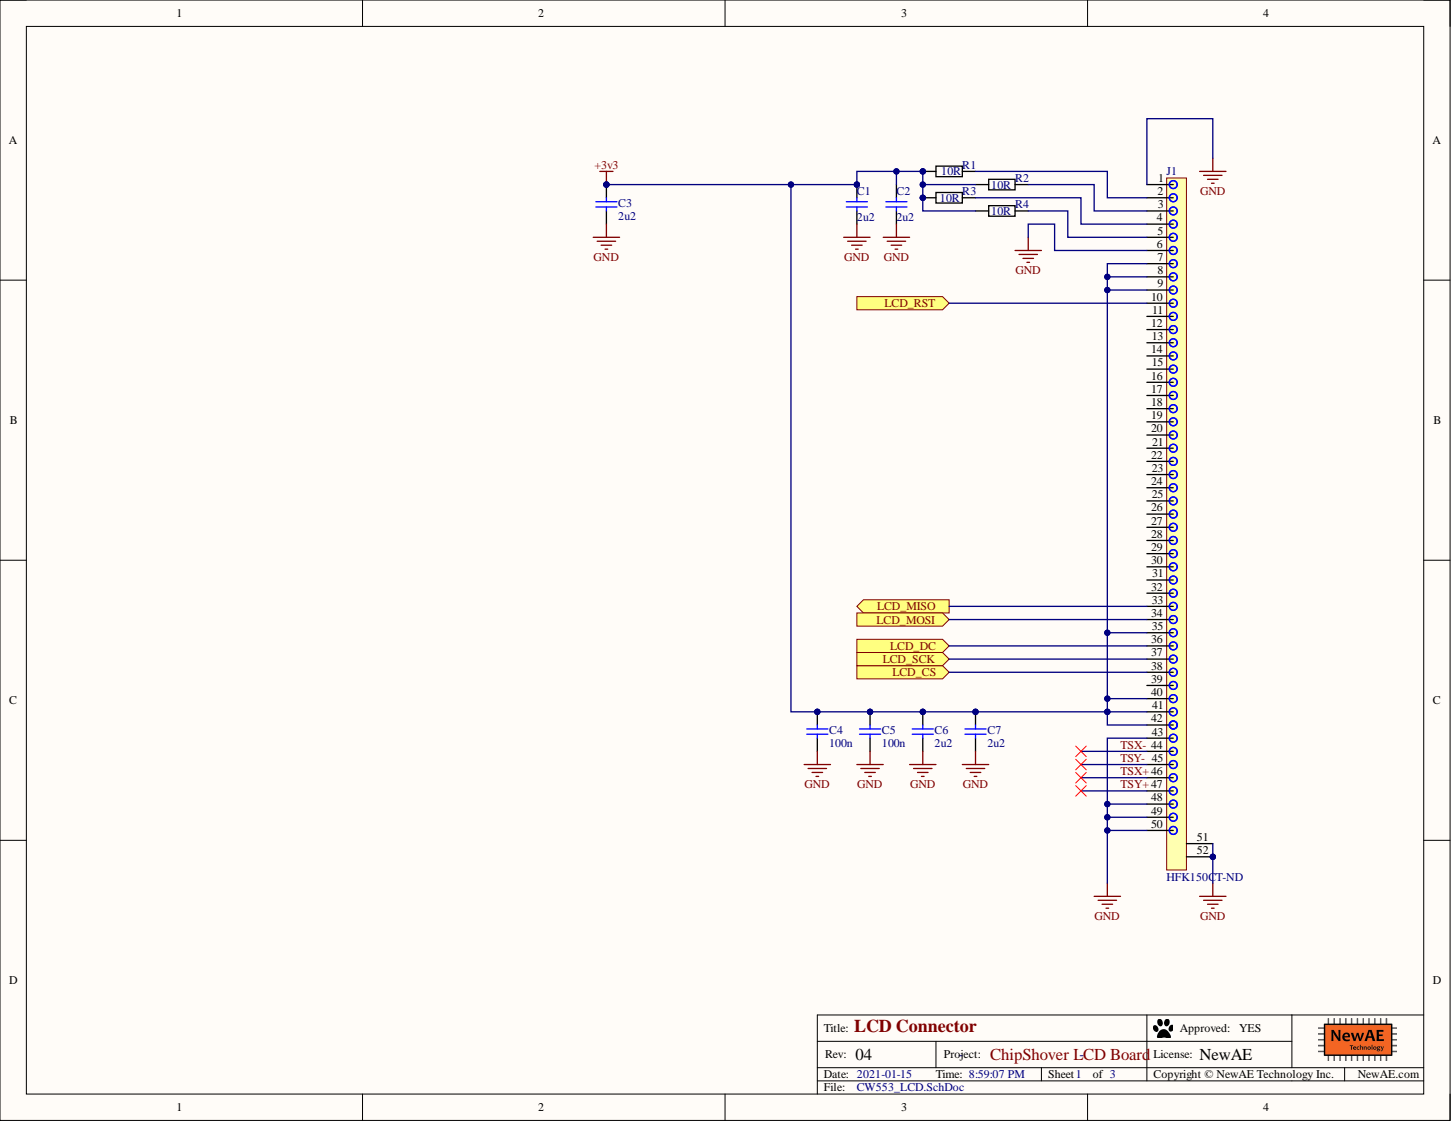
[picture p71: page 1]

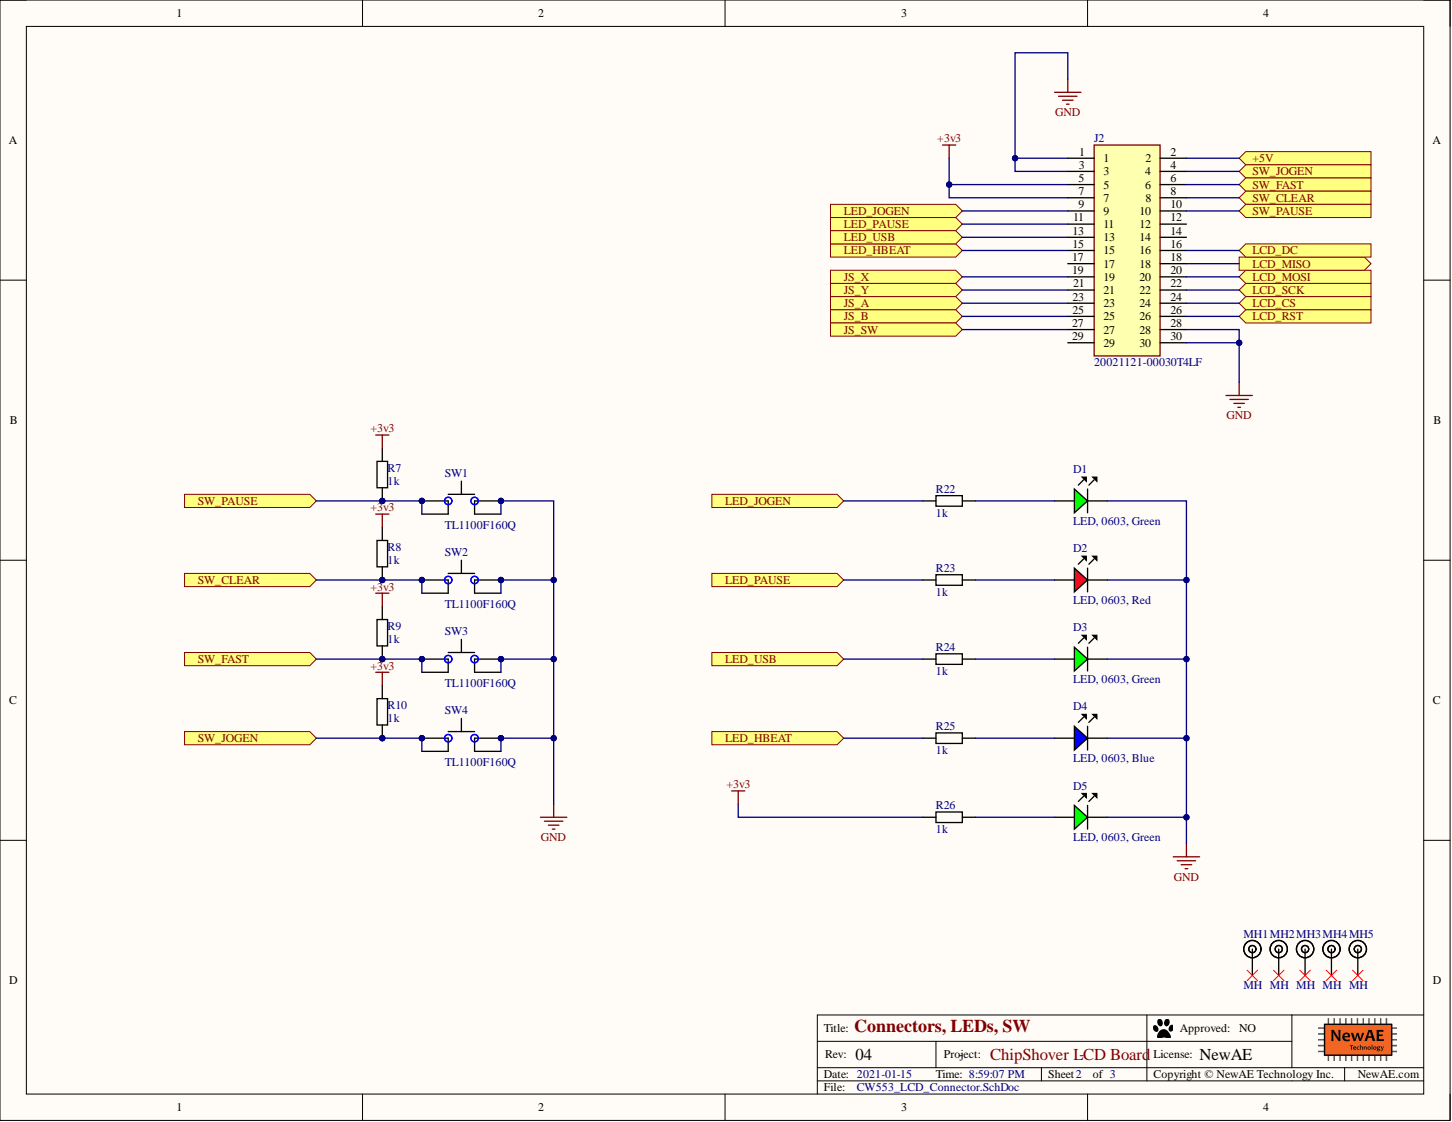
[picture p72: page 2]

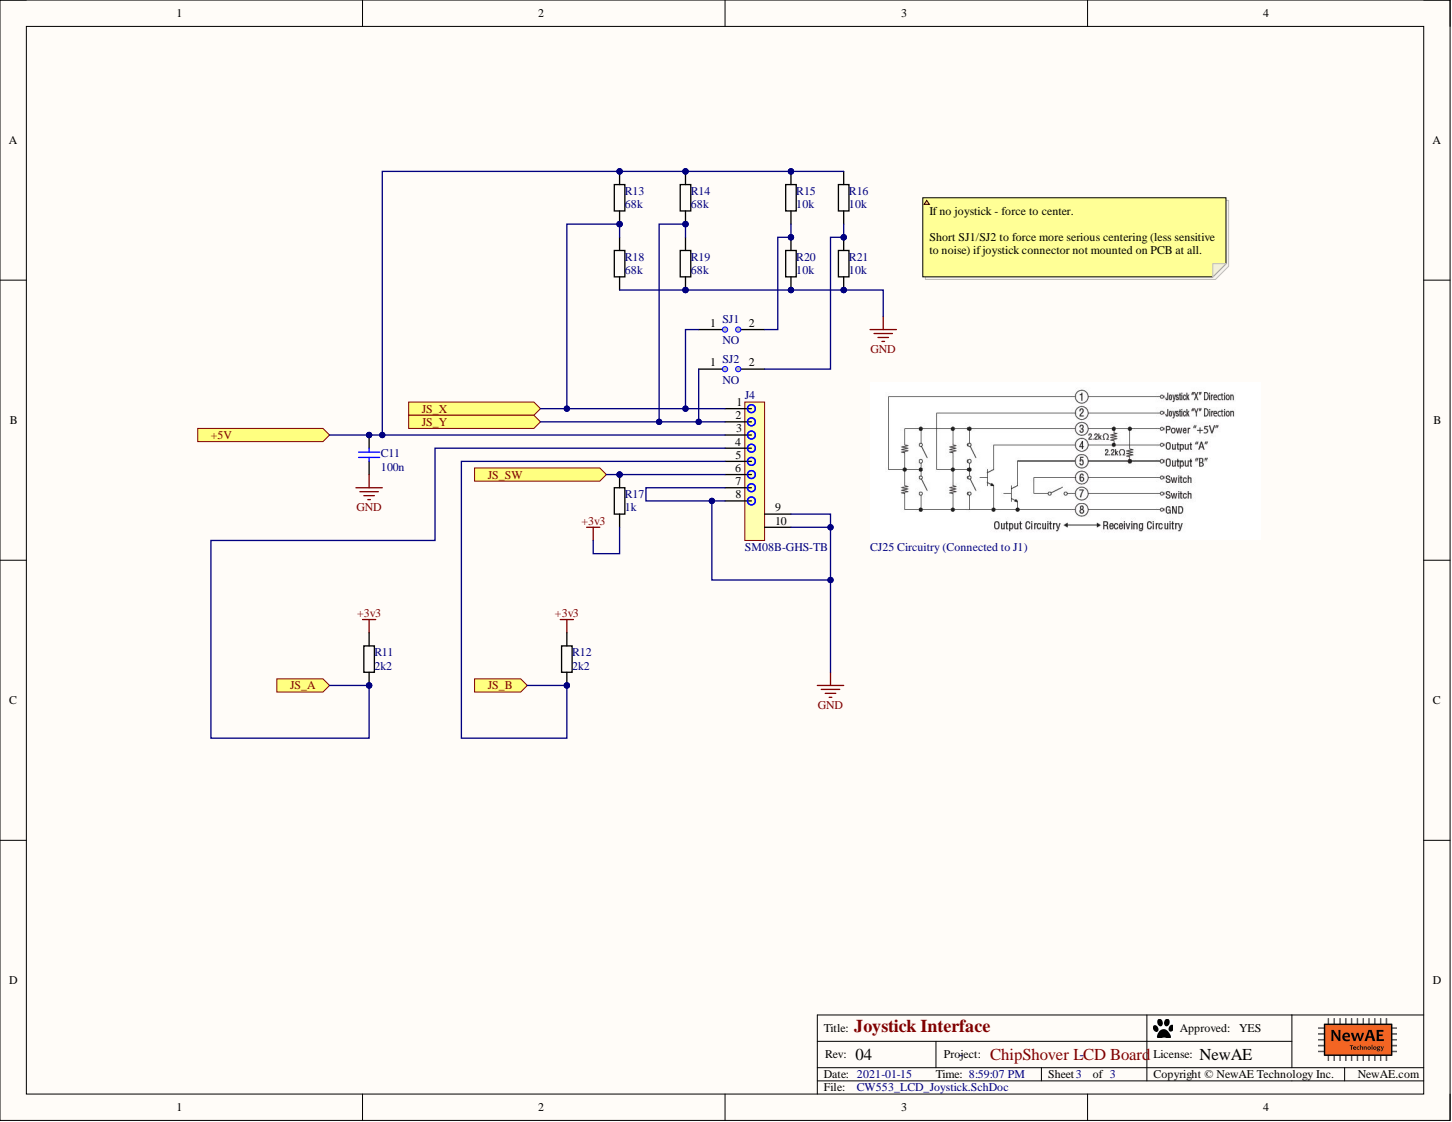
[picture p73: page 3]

If no joystick - force to center.

Short SJ1/SJ2 to force more serious centering (less sensitive
to noise) if joystick connector not mounted on PCB at all.

10

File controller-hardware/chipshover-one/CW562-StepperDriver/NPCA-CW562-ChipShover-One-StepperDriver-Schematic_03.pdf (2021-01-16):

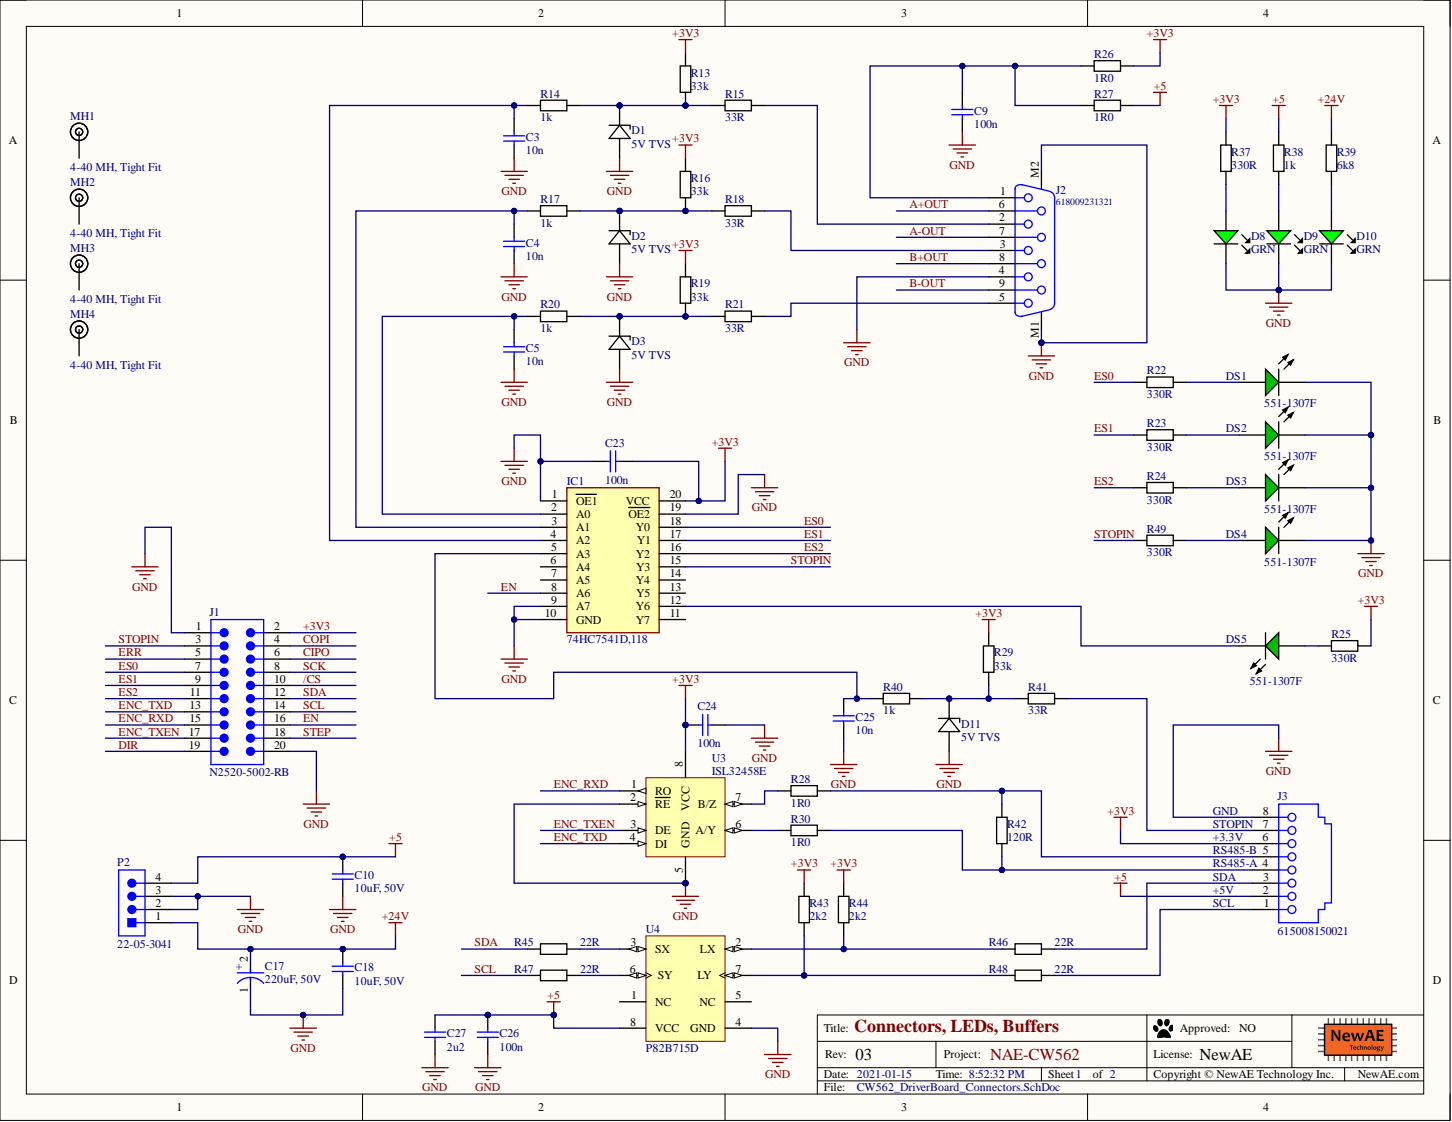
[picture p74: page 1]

A7 9
GND 10 | +3V3


From Datasheet:
Pins 1, 33, 20, 34 are not
internally connected.
Datasheet suggets connect
them as helpful for routing
purposes!

Suggests connecting 1/33 to
VSA/VSB for example to
allow wider traces.

SW1 sets I2C address so each
board has a diff temp sensor
address. Should have
silkscreen mark showing
X/Y/Z settings.


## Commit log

2020-09-07 Read step count from driver board
2020-09-10 Add fan control
2020-12-22 Update readme, add schematic
2021-01-16 Add schematics for boards
2021-01-18 Add link to marlin2
2021-01-18 Move schematics around, add CW554
2021-01-21 Add frame/box removal
2021-01-27 Add more debug info in case problem with get_position(), add flush to fix issue #2 hopefully
2021-01-30 Fix wrong endstop description
2021-01-31 Add stages readme
2021-02-02 Add STL + source files for the mounting brackets
    [3020Table_ChipShouterAdapter_HardwareNeeded.f3d, 3020Table_ChipShouterAdapter_HardwareNeeded.stl, 3020Table_ChipShouterAdapter_NoHardwareNeeded.f3d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]
2021-02-02 Fix low res stage docs
2022-09-12 Fix fan numbering
2022-12-06 Add initial holder designs
    [chipshouter mount - M3 or 4-40 holding bolt.f3d, chipshouter mount - M3 or 4-40 holding bolt.step, chipshouter mount - M3 or 4-40 holding bolt.stl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]
2023-02-02 Update assembly instructions
